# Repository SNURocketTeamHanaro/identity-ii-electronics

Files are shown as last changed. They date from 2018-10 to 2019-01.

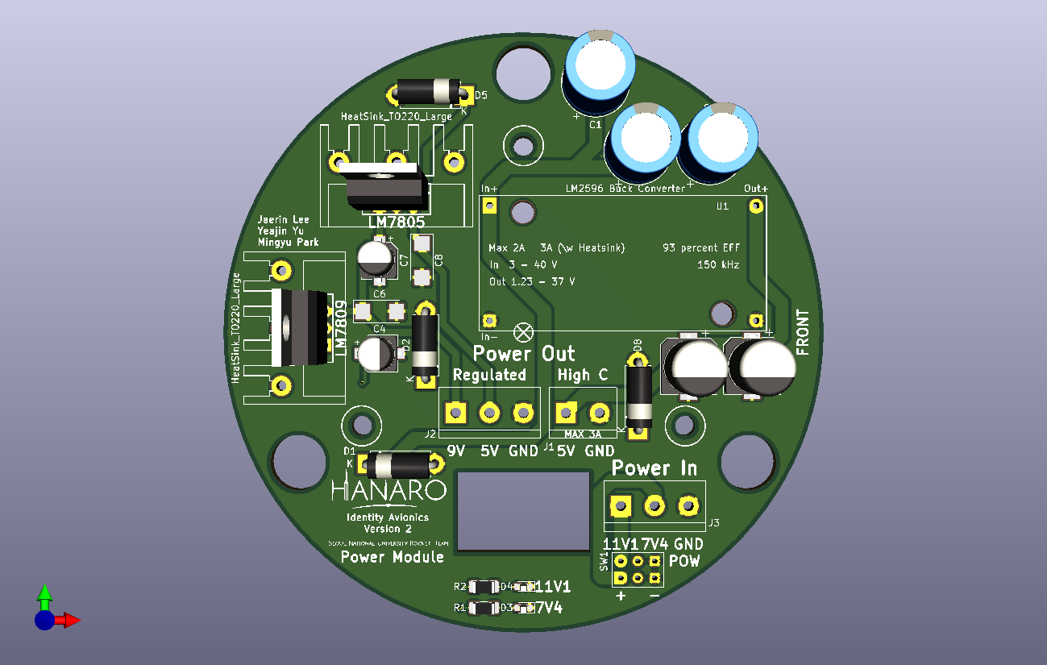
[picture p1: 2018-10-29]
power.png

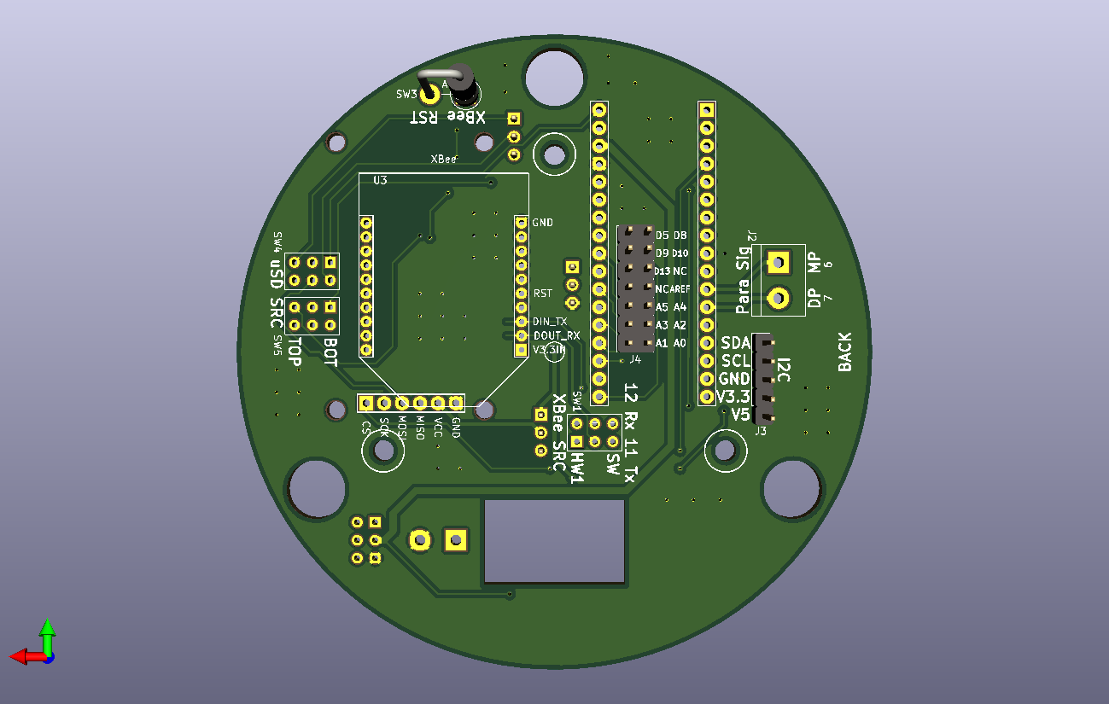
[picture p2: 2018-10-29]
core-back.png

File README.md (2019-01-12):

# Identity-II Electronics
Electrical hardware of data acquisition and control system of Identity-II rocket

### Specification
1. Data Acquisition
   - Altitude measurement via [BMP280](https://cdn-shop.adafruit.com/datasheets/BST-BMP280-DS001-11.pdf)
   - 3-Axis Accelerometer, 3-Axis Gyroscope, 3-Axis Magnetometer reads data in every cycle
   - System time is recorded with the data
   - All the data measurements are taken in every 5-7 ms
   - Raspberry Pi camera module saves the recorded image automatically after the power is on
1. Communication
   - Zigbee communication is tested to reach 1000m without severe interference
   - Baud rate of 38400 is used for serial communication with the XBee module; At higher rate, some Arduino chips are not able to handle the speed of the signal alternation
   - Rocket status code along with the current altitude and time is sent via Zigbee channel
1. Control
   - Drogue parachute ejection at the peak altitude; Simple peak detection
   - Main parachute ejection in two modes
     1. Relative altitude mode (Max. Alt. < 390m): Main parachute ejection at "alt. = max. alt. - 70m"
     2. Absolute altitude mode (Max. Alt. > 390m): Main parachute ejection at "alt. = 320m"
1. Others
   - Additional 6 analog pins of Arduino Micro core can be reachable at the back of the core module

### Additional Requirements
#### Hardware
- Li-Po battery 3.7V, minimum 2000 mAh (x3)
- [Buck converter 5V output, minimum 2A (x1)](https://www.amazon.com/eBoot-LM2596-Converter-3-0-40V-1-5-35V/dp/B01GJ0SC2C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)
- Arduino Micro (x1)
- Digi XBee-Pro (x1)
- [MicroSD card adapter (x1)](https://www.amazon.com/SenMod-Adapter-Reader-Module-Arduino/dp/B01JYNEX56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) (You may use other boards) 
- [GY-91 IMU sensor (x1)](https://www.amazon.com/WINGONEER-MPU9250-Acceleration-Gyroscope-Compass/dp/B06XHJQKT6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)
- L293B (x1)
- Raspberry Pi 3 or high (x1)
- PiCamera for RPi (x1)
- Power switch (x1)
- Some terminal blocks
- Some hexagonal supporters, 3-phi
#### Software
- Arduino source code ()
- Data decoder code ()

### Installation
There are three PCB layers with additional battery mount assembled in the following order:  
(top)  
battery  
power module  
core module  
imu module  
RPi Camera and Power button mount  
RPi  
![Full mount]()

### Credit
[Jaerin Lee](https://github.com/ironjr)  
Lead Electronics and Software Developer  
SNU Rocket Team Hanaro

Documented with KiCAD version 5.0.0

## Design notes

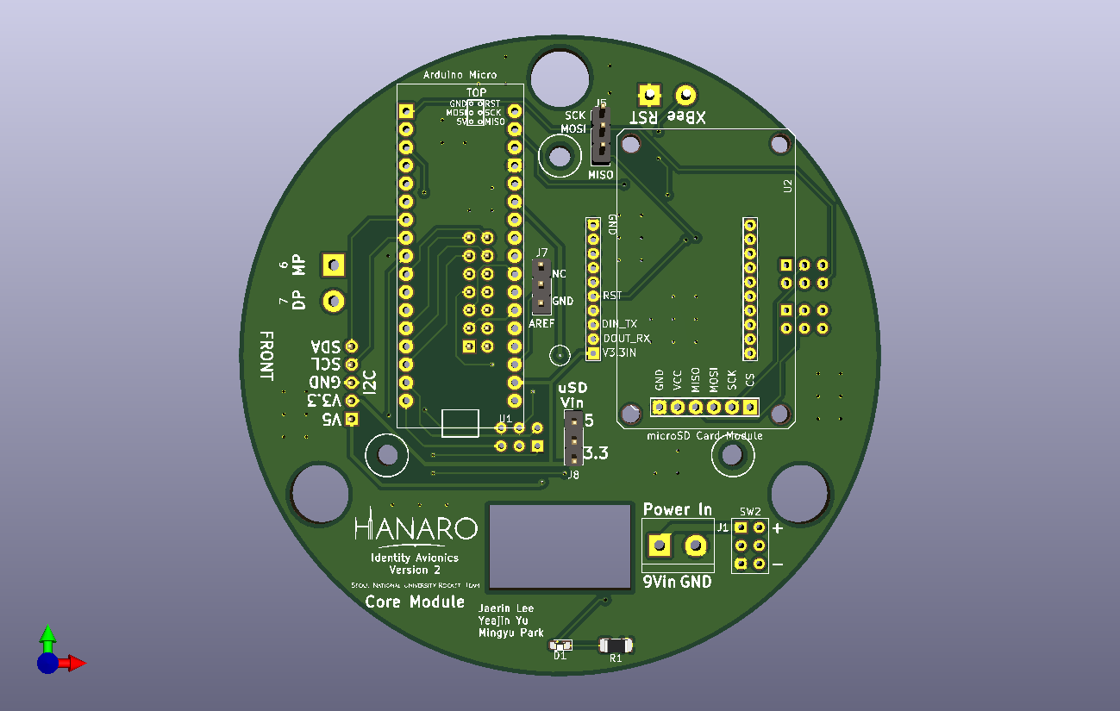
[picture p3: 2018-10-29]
core.png

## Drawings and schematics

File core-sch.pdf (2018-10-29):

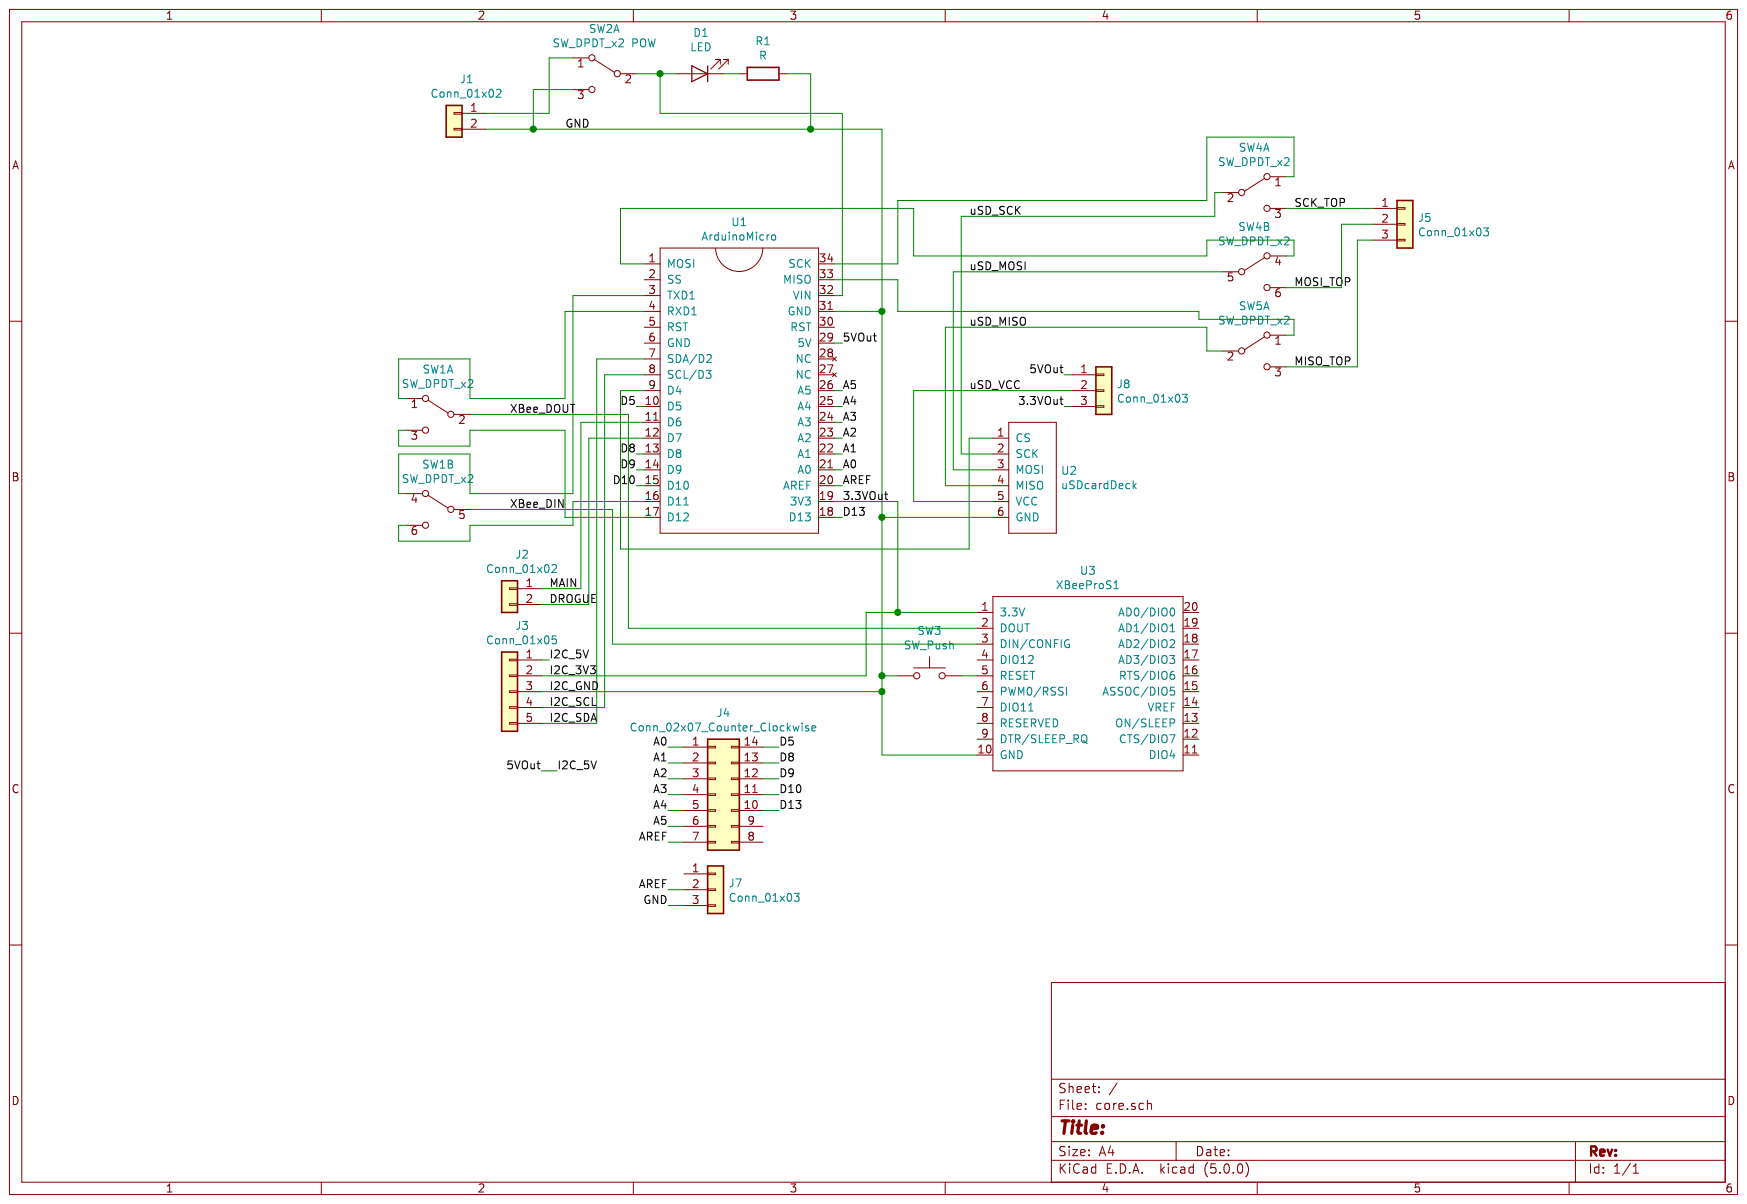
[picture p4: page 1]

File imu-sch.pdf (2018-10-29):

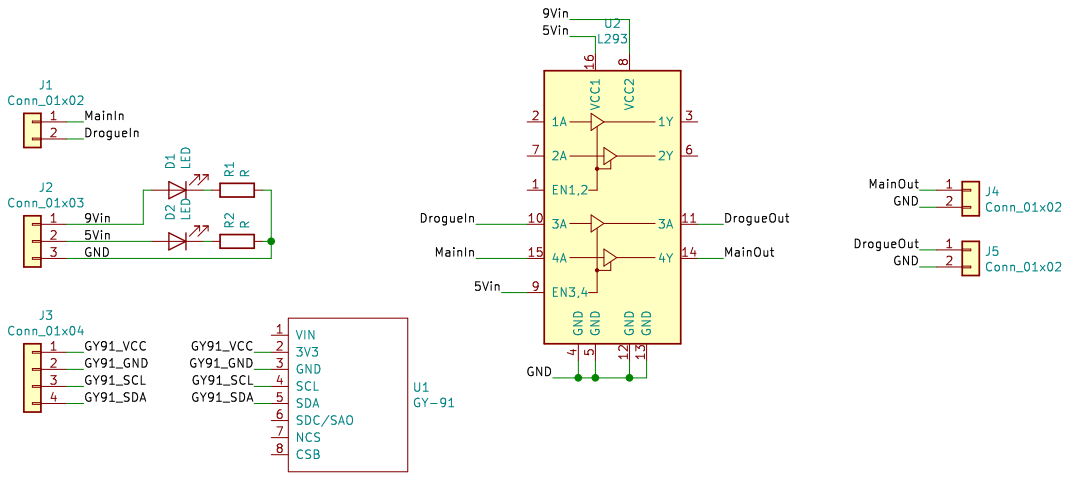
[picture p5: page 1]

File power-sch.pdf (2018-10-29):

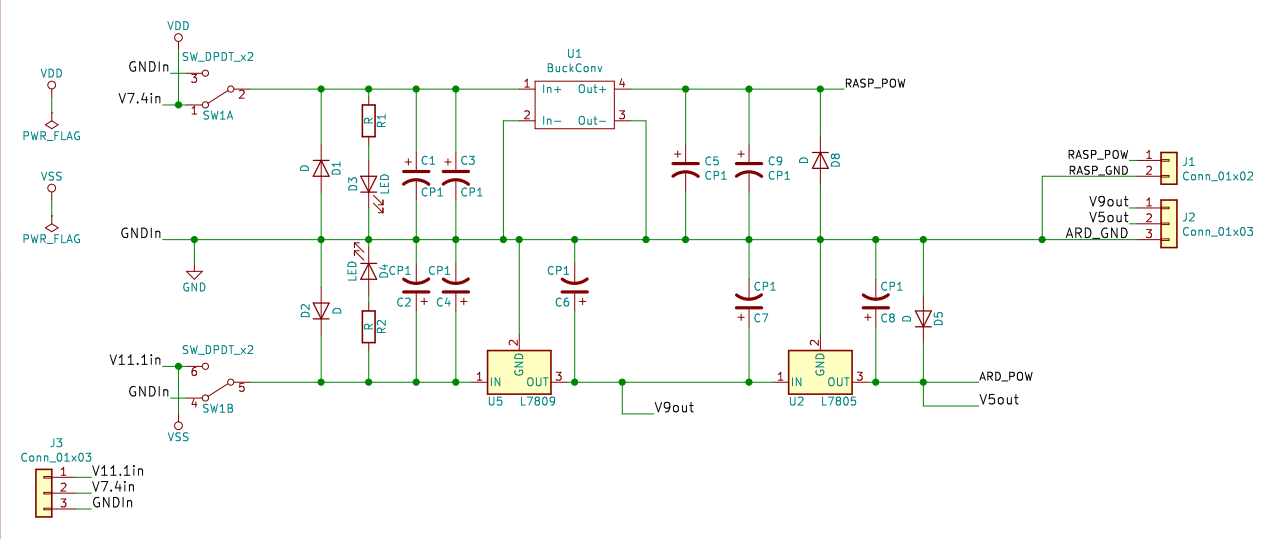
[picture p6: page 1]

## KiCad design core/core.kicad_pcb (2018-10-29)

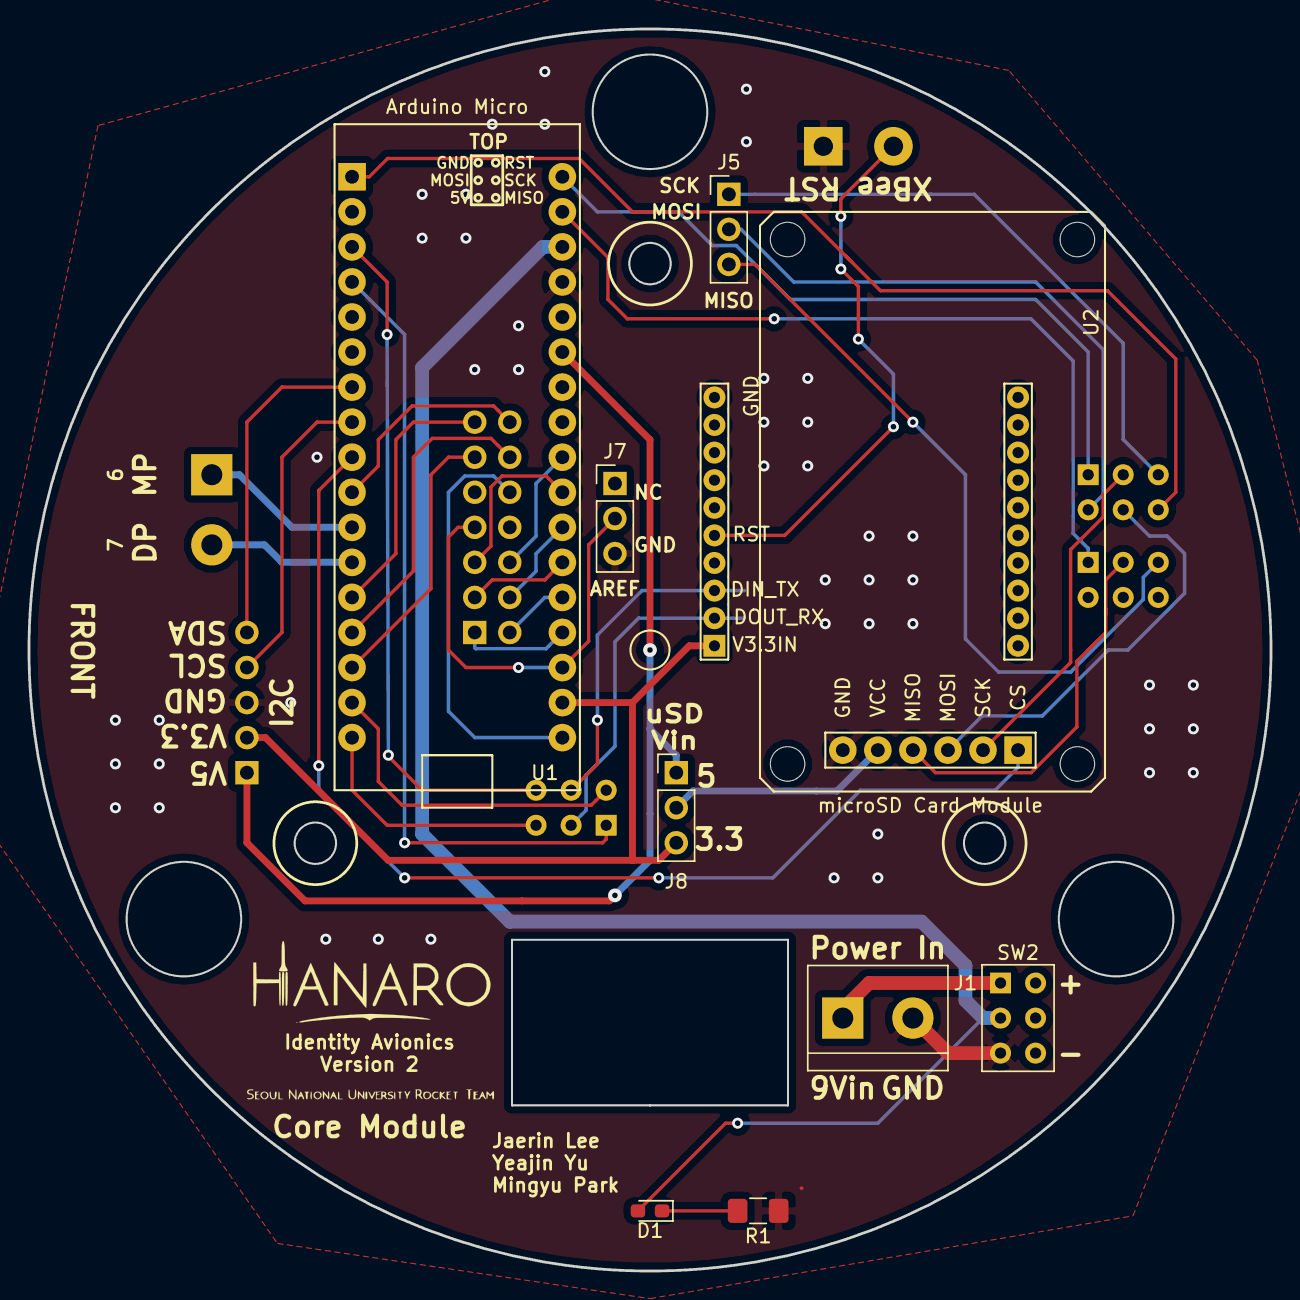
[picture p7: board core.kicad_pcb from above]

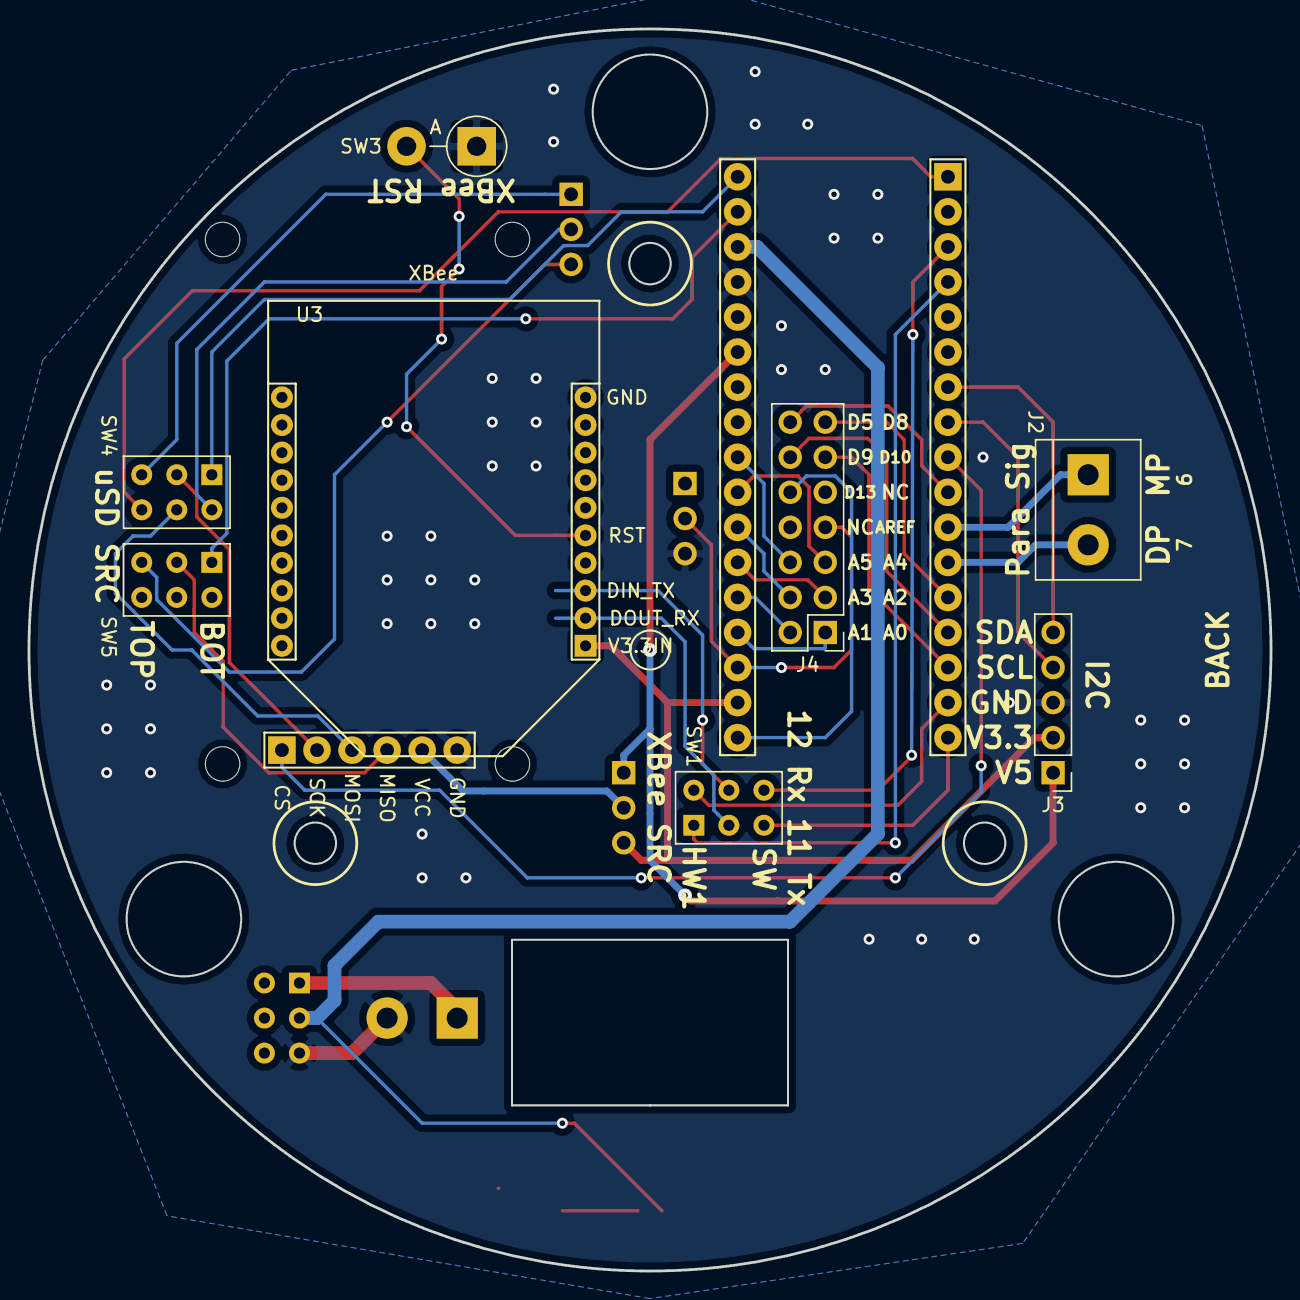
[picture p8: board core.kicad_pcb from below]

Board: 2 copper layers, 90.0 x 90.0 mm, 17 parts (8 on the bottom side), 40 nets.

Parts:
D1: LED; LED_0603_1608Metric_Pad1.05x0.95mm_HandSolder
J1, J2: Conn_01x02; TerminalBlock_bornier-2_P5.08mm
J3: Conn_01x05; Pin_Header_Straight_1x05_Pitch2.54mm
J4: Conn_02x07_Counter_Clockwise; Pin_Header_Straight_2x07_Pitch2.54mm
J5, J7, J8: Conn_01x03; Pin_Header_Straight_1x03_Pitch2.54mm
R1: R; R_1206_3216Metric_Pad1.42x1.75mm_HandSolder
SW1, SW4, SW5: SW_DPDT_x2; SW_NKK_G1xJP
SW2: SW_DPDT_x2 POW; SW_NKK_G1xJP
SW3: SW_Push; D_5W_P5.08mm_Vertical_AnodeUp
U1: ArduinoMicro; Arduino_Micro
U2: uSDcardDeck; uSDcard_Type_1
U3: XBeeProS1; XBee

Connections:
/3.3VOut: J3.2, J8.3, U1.19, U3.1
/5VOut: J3.1, J8.1, U1.29
/A0: J4.1, U1.21
/A1: J4.2, U1.22
/A2: J4.3, U1.23
/A3: J4.4, U1.24
/A4: J4.5, U1.25
/A5: J4.6, U1.26
/AREF: J4.7, J7.2, U1.20
/D5: J4.14, U1.10
/D8: J4.13, U1.13
/D9: J4.12, U1.14
/D10: J4.11, U1.15
/D13: J4.10, U1.18
/DROGUE: J2.2, U1.12
/GND: J1.2, J3.3, J7.3, R1.1, SW2.3, SW3.1, U1.31, U2.6, U3.10
/I2C_SCL: J3.4, U1.8
/I2C_SDA: J3.5, U1.7
/MAIN: J2.1, U1.11
/MISO_TOP: J5.3, SW5.3
/MOSI_TOP: J5.2, SW4.6
/SCK_TOP: J5.1, SW4.3
/XBee_DIN: SW1.5, U3.3
/XBee_DOUT: SW1.2, U3.2
/uSD_MISO: SW5.2, U2.4
/uSD_MOSI: SW4.5, U2.3
/uSD_SCK: SW4.2, U2.2
/uSD_VCC: J8.2, U2.5
unnamed: D1.1, R1.2
unnamed: D1.2, SW2.2, U1.32
unnamed: J1.1, SW2.1
unnamed: SW1.1, U1.4
unnamed: SW1.3, U1.17
unnamed: SW1.4, U1.3
unnamed: SW1.6, U1.16
unnamed: SW3.2, U3.5
unnamed: SW4.1, U1.34
unnamed: SW4.4, U1.1
unnamed: SW5.1, U1.33
unnamed: U1.9, U2.1

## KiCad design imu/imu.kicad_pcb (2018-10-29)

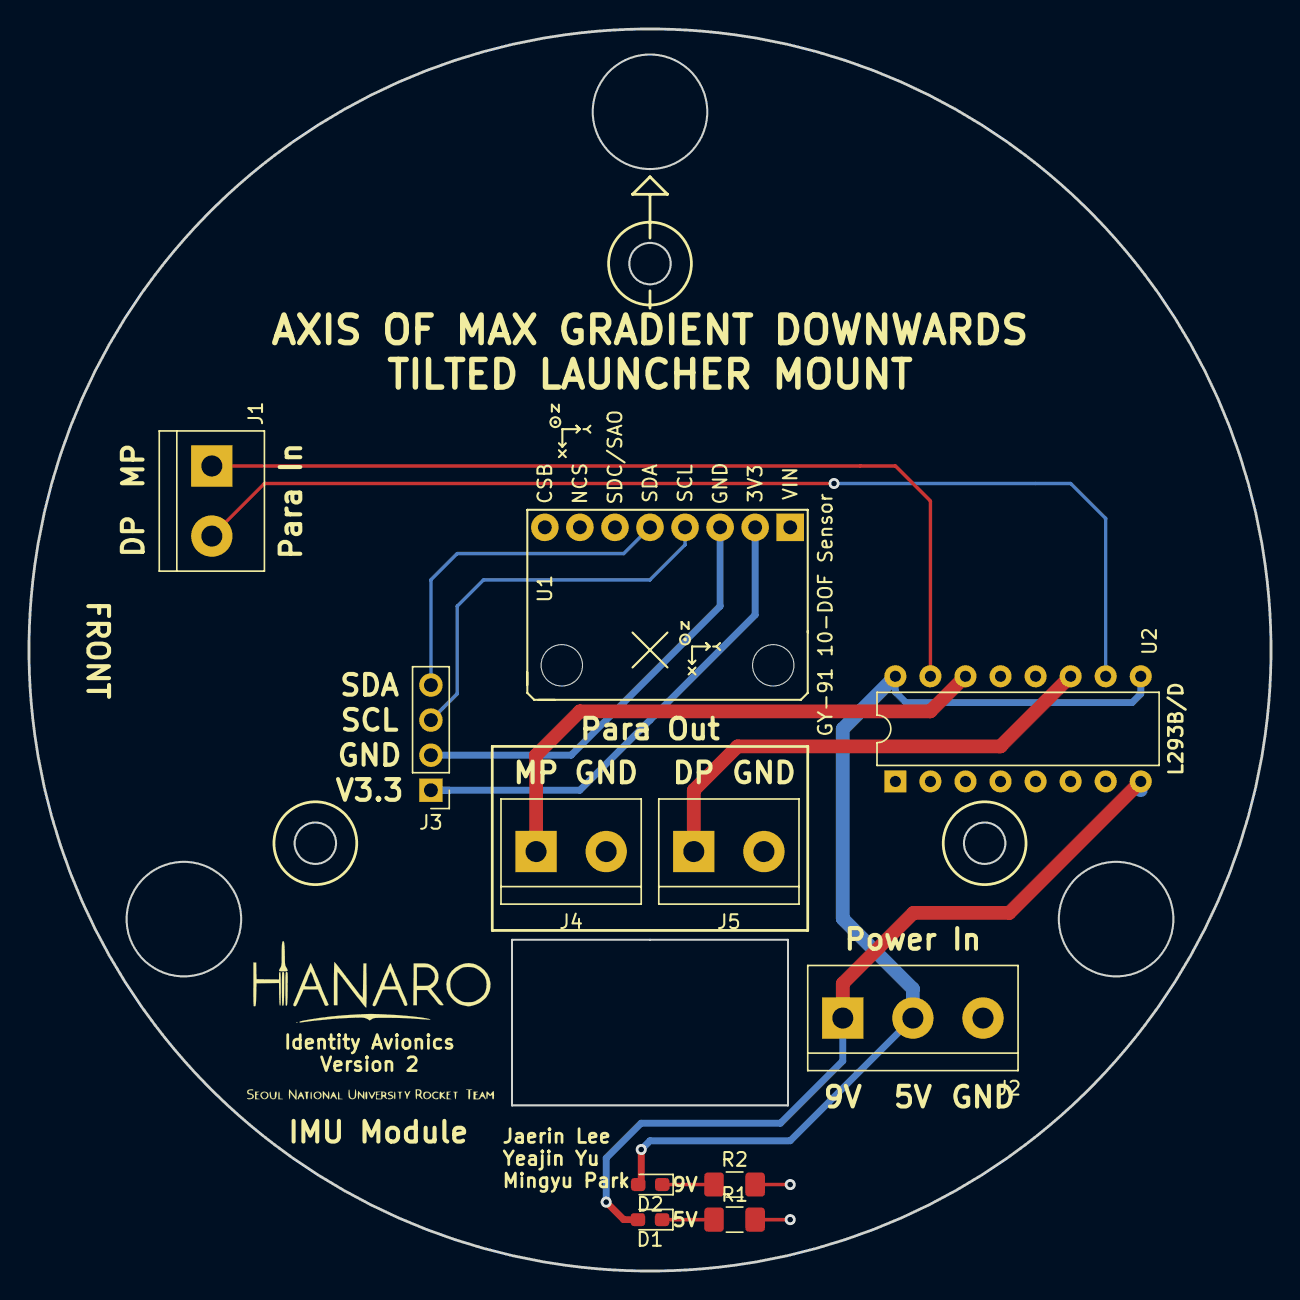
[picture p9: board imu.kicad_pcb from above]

Board: 2 copper layers, 90.0 x 90.0 mm, 11 parts (0 on the bottom side), 13 nets.

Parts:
D1, D2: LED; LED_0603_1608Metric_Pad1.05x0.95mm_HandSolder
J1, J4, J5: Conn_01x02; TerminalBlock_bornier-2_P5.08mm
J2: Conn_01x03; TerminalBlock_bornier-3_P5.08mm
J3: Conn_01x04; PinHeader_1x04_P2.54mm_Vertical
R1, R2: R; R_1206_3216Metric_Pad1.42x1.75mm_HandSolder
U1: GY-91
U2: L293; DIP-16_W7.62mm

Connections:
/5Vin: D2.2, J2.2, U2.9, U2.16
/9Vin: D1.2, J2.1, U2.8
/DrogueIn: J1.2, U2.10
/DrogueOut: J5.1, U2.11
/GND: J2.3, J4.2, J5.2, R1.2, R2.2, U2.4, U2.5, U2.12, U2.13
/GY91_GND: J3.2, U1.3
/GY91_SCL: J3.3, U1.4
/GY91_SDA: J3.4, U1.5
/GY91_VCC: J3.1, U1.2
/MainIn: J1.1, U2.15
/MainOut: J4.1, U2.14
unnamed: D1.1, R1.1
unnamed: D2.1, R2.1

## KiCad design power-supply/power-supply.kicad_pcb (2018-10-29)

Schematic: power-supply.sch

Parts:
C1, C2, C3: CP1; CP_Radial_D10.0mm_P5.00mm
C4, C7: CP1; CP_Elec_5x5.3
C5, C9: CP1; CP_Elec_8x10
C6, C8: CP1; CP_EIA-6032-20_AVX-F_Pad2.25x2.35mm_HandSolder
D1, D2, D5, D8: D; D_5W_P10.16mm_Horizontal
D3, D4: LED; LED_0603_1608Metric_Pad1.05x0.95mm_HandSolder
J1: Conn_01x02; TerminalBlock_bornier-2_P5.08mm
J2, J3: Conn_01x03; TerminalBlock_bornier-3_P5.08mm
R1, R2: R; R_1206_3216Metric_Pad1.42x1.75mm_HandSolder
SW1: SW_DPDT_x2; SW_NKK_G1xJP
U1: BuckConv; Buck_Converter_LM2596_3A
U2: L7805; TO-220-3_Vertical
U5: L7809; TO-220-3_Vertical

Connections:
/ARD_POW: C8.1, D5.1, J2.2, U2.3 (OUT)
/RASP_POW: C5.1, C9.1, D8.1, J1.1, U1.4
/V9out: C6.1, C7.1, J2.1, U2.1 (IN), U5.3 (OUT)
GND: C1.2, C2.2, C3.2, C4.2, C5.2, C6.2, C7.2, C8.2, C9.2, D1.2, D2.2, D3.1, D4.1, D5.2, D8.2, J1.2, J2.3, J3.3, SW1.3 (C), SW1.4 (A), U1.2, U1.3, U2.2 (GND), U5.2 (GND)
unnamed: C1.1, C3.1, D1.1, R1.1, SW1.2 (B), U1.1
unnamed: C2.1, C4.1, D2.1, R2.2, SW1.5 (B), U5.1 (IN)
unnamed: D3.2, R1.2
unnamed: D4.2, R2.1
VDD: J3.2, SW1.1 (A)
VSS: J3.1, SW1.6 (C)

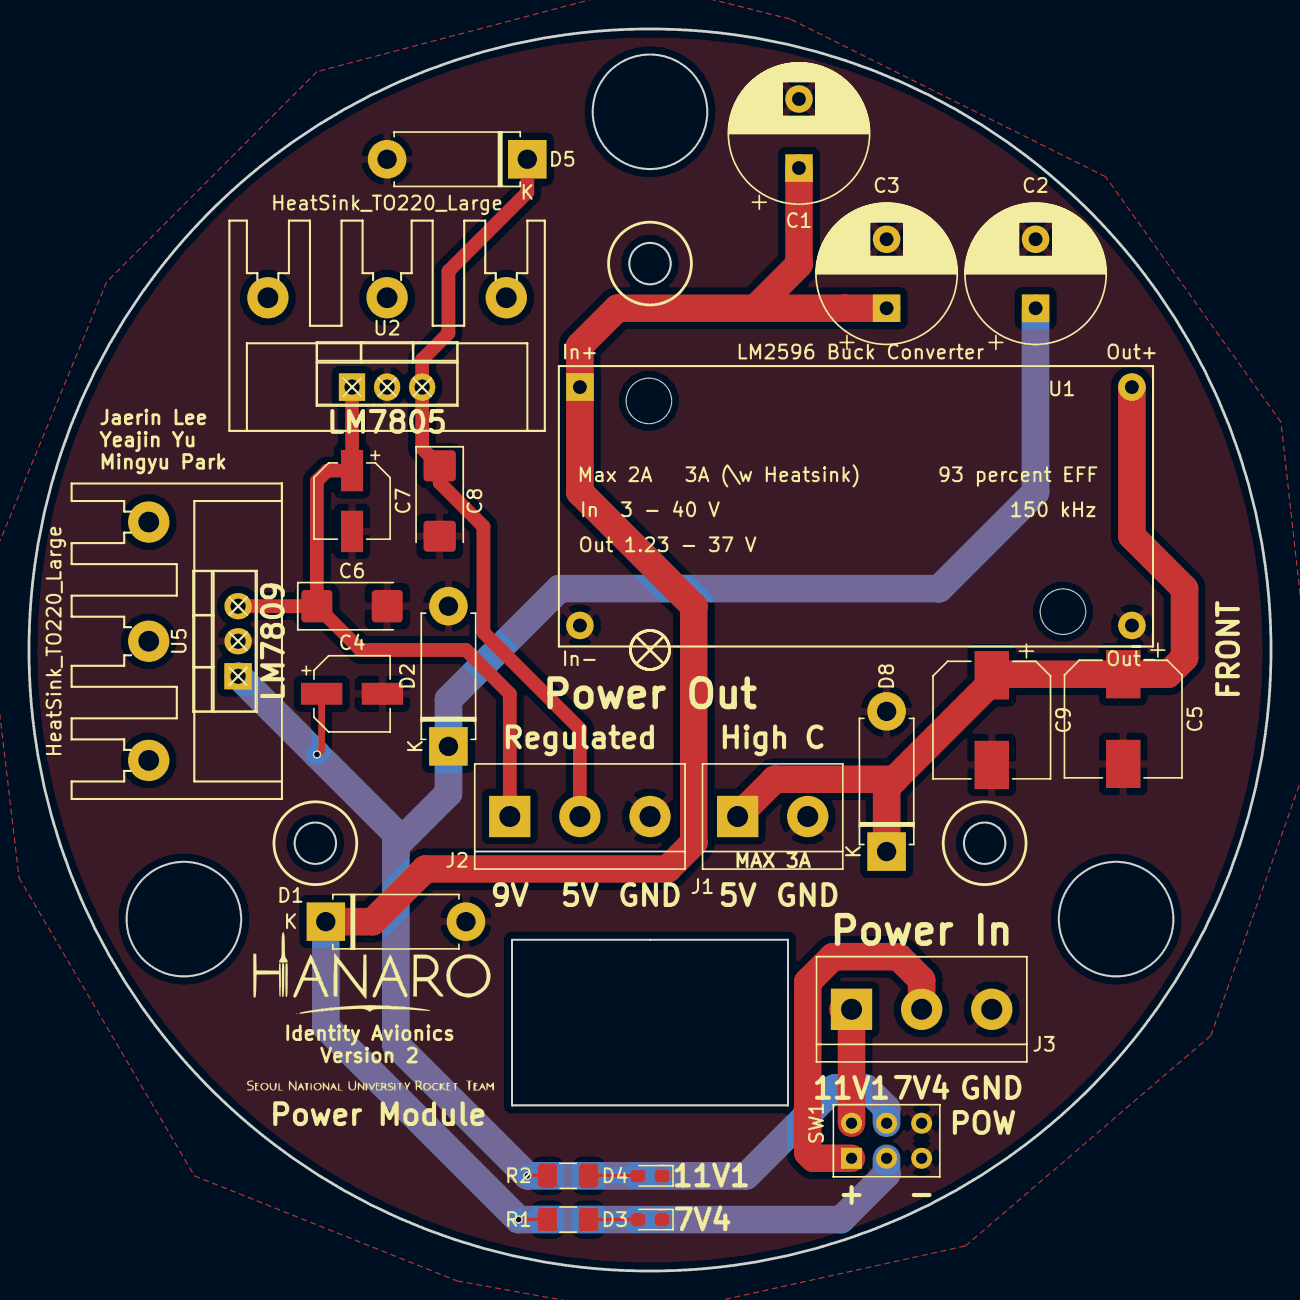
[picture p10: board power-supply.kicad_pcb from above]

Board: 2 copper layers, 90.0 x 90.0 mm, 24 parts (0 on the bottom side), 10 nets.
